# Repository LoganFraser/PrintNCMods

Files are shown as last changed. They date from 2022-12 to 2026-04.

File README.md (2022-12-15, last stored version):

# PrintNCMods
My design files for the PrintNC CNC machine

Logan BC CA - Logan#2225 on Three Design - PrintNC Discord
https://discord.gg/fXqRkUTsUD

If you like my work and want to buy me a beer (or coffee),  
you can use this [Paypal](https://www.paypal.com/donate/?hosted_button_id=QBMAY9ZB6N3F8) link    
or this QR code:  
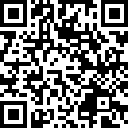
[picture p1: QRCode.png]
QRCode


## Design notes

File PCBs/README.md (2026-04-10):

## A collection of PCBs for the PrintNC compatible with various controllers ##

I sell kits for the driver key PCBs that include IDC cable, connectors, jacks and pins (5 for $20 CAD, $10 for assembly, + shipping) and a kit with the toolhead and gantry PCBs that include screw terminals, ethernet jacks ($30 CAD, $10 for assembly, + shipping) though the PrintNC Discord https://discord.gg/rXNhba3C @logan2225

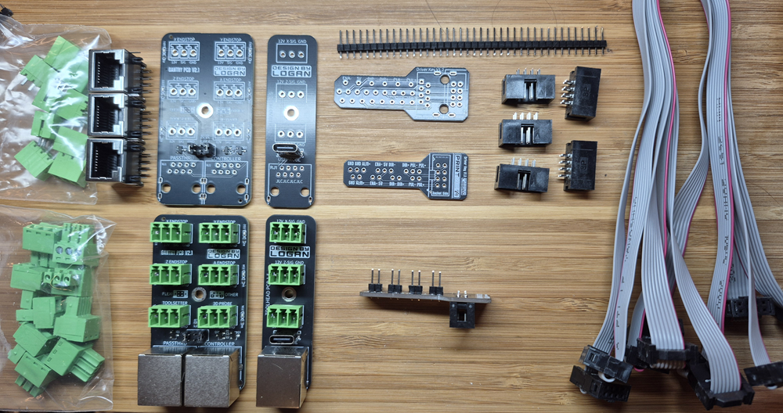
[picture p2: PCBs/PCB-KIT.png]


### Fusion 360 and Step CAD files for 3d Printed Enclosures and Soldering Guides ###
Cad files are here: https://github.com/LoganFraser/PrintNCMods/tree/main/PCBs/CAD_Sensor_PCB_Cases

### Driver Key PCB ###
A convenient method to connect the Flexihal to the DM542T/DM556T or other drivers.

Version 1.3 here: https://github.com/LoganFraser/PrintNCMods/tree/main/PCBs/Driver_Key_1.3_PCB

Version 1.2 here: https://github.com/LoganFraser/PrintNCMods/tree/main/PCBs/Driver_Key_1.2_PCB

Assembly - Use the row of pins that matches your screw terminal spacing on your stepper drivers. 
Most current open loop drivers and closed loop drives without a brake input will use the 3.81mm spacing screw terminals.  
It will be marked on one end - 3.5 or 3.81 or 5.08.  Be careful to place the IDC connector on the same side as the outline
and with the notch lined up with the silkscreen - facing away from the pins for 1.2, and towards the pins for 1.3

### Endstop PCBs: ###
a collection of pcbs that provide various functions as follows: 

### Gantry Sensor PCB ### 
 
Updated with bypass jumpers to remove the inverting effect of the LED isolation circuit for the Flexihal

https://github.com/LoganFraser/PrintNCMods/tree/main/PCBs/Gantry_Sensor_PCB_2.1

### Toolhead Sensor PCB ###
for connecting X/Z axis and 3d probe at the toolhead to minimize individual cables in the cablechain.  

https://github.com/LoganFraser/PrintNCMods/tree/main/PCBs/Toolhead_Sensor_PCB_1.5

### Sensor Endstop Cabinet PCB ###
for connecting the cabinet end of the ethernet cable. Not needed for connection to GrblHal2k EST or FlexiHAL controllers.

https://github.com/LoganFraser/PrintNCMods/tree/main/PCBs/Enclosure_Sensor_PCB

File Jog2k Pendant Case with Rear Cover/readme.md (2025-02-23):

This modifies the great case by mikemacwillie from here: 

https://github.com/Expatria-Technologies/Mods-Accessories/tree/main/Expatria/Jog2K_Deluxe

I've moved the cover to the rear of the case to make it easier to install the screen and heatset screw inserts.  

There's a screen brace that holds the screen into the case.

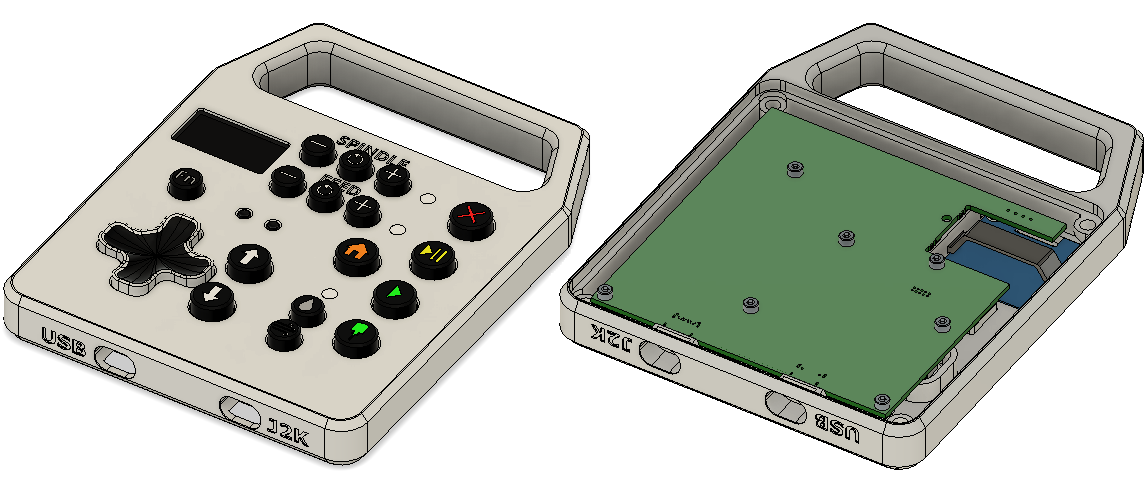
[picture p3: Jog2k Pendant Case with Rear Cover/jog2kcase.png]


This is a collection of mounts for storage of the jog2k, button pcb, and wireless or small keyboard (I use a Logitech K400)

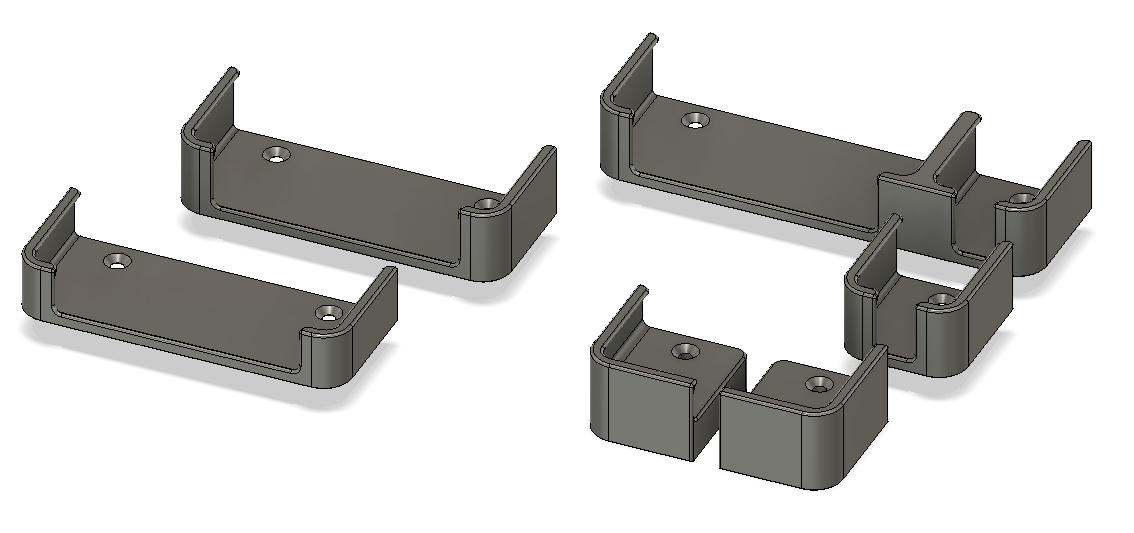
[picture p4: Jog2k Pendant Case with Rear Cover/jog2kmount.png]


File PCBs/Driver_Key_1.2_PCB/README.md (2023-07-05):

## Driver Key PCB for DM542T and DM556T

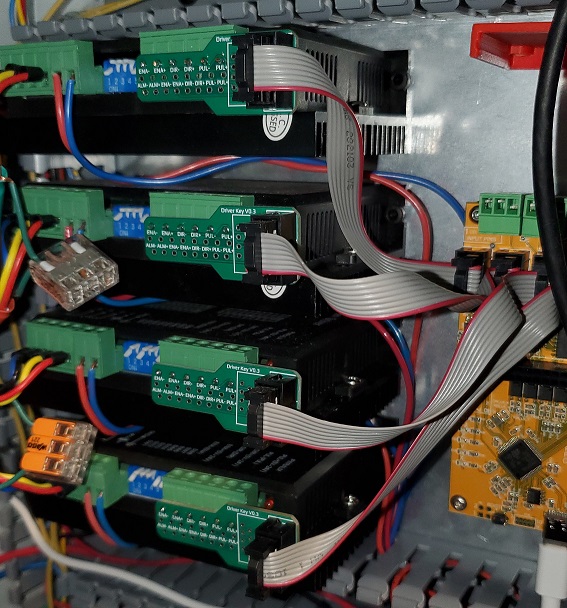
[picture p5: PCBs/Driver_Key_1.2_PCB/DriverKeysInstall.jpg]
Driver Keys Install


Goal: To provide a simple connection method from Flexihal or Grblhal 2000 IDC outputs to external drivers.

# Assembly: 

First solder the IDC 8 pin connector to the PCB, matching the silkscreen notch to the connector notch.  
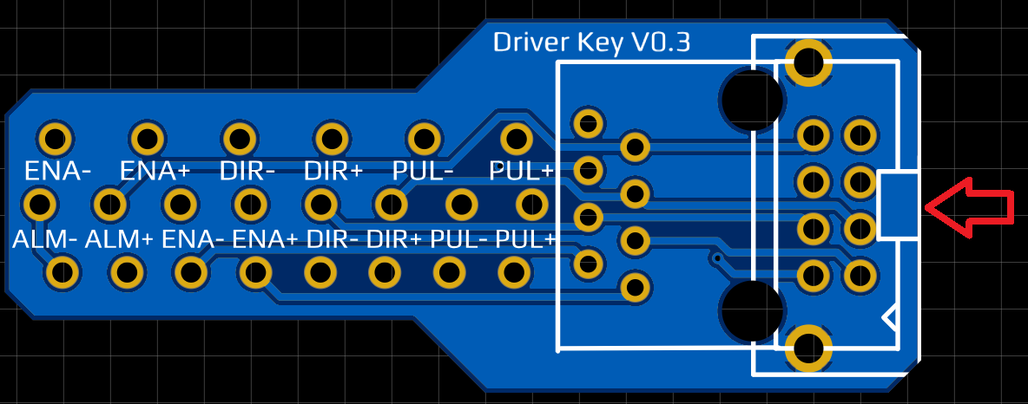
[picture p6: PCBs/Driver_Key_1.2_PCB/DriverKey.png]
DriverKey


Next remove the plugin screw terminal from the driver that has Enable, Direction and Pulse/Step inputs on it.  

Cut short pieces of 0.5mm^2/20AWG of bare(stripped) solid core wire 10mm or 3/8" long, insert into the Dir +/- and Step +/- screw terminal block and tighten the screws.

Next align the wires with the holes on the pcb that match the correct spacing, and solder in place.
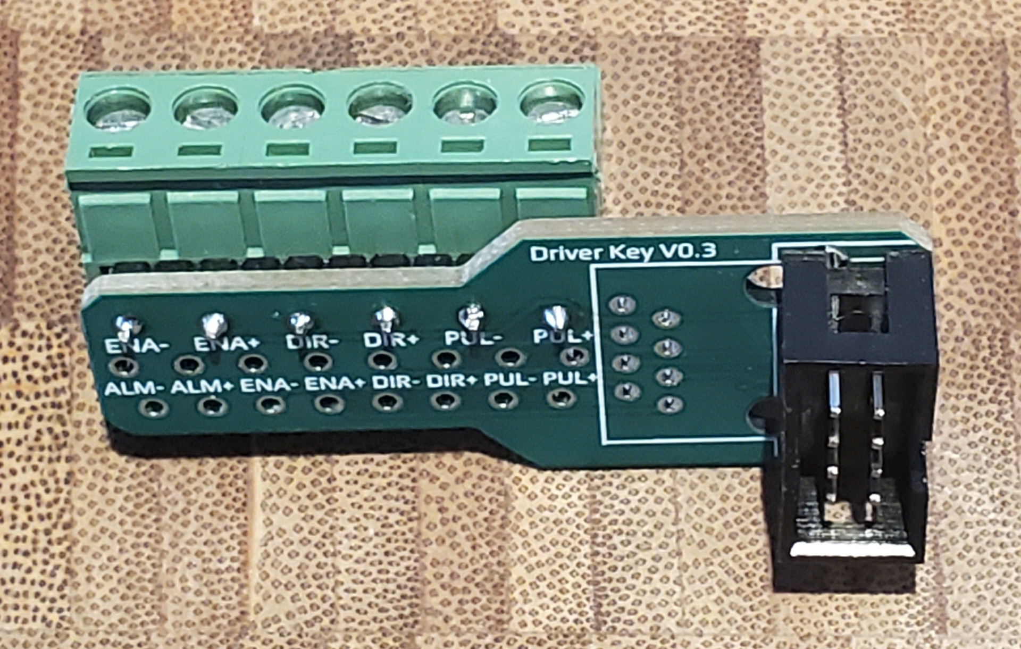
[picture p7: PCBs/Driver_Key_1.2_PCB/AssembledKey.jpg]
AssembledKey


Optional: Add wires for Enable and/or Error to the driver.  Currently neither is recommended for inital setup as it just adds confusion and doesn't provide a benefit with DM542T or DM556T drivers. 

Follow this guide to assemble the IDC cables, taking care to match the faint arrow with the red wire on both ends.  Use of a vice isn't required for 8pin idc, though, you can just press them together with a block of wood or metal on a countertop.  [IDC ribbon Cable Guide](https://startingelectronics.org/articles/IDC-ribbon-cable/)

Enjoy!  

As a bonus, here are the default jumpper settings for the PrintNC with 100 steps/mm for XYZ and 3A kit steppers on printed mounts.  

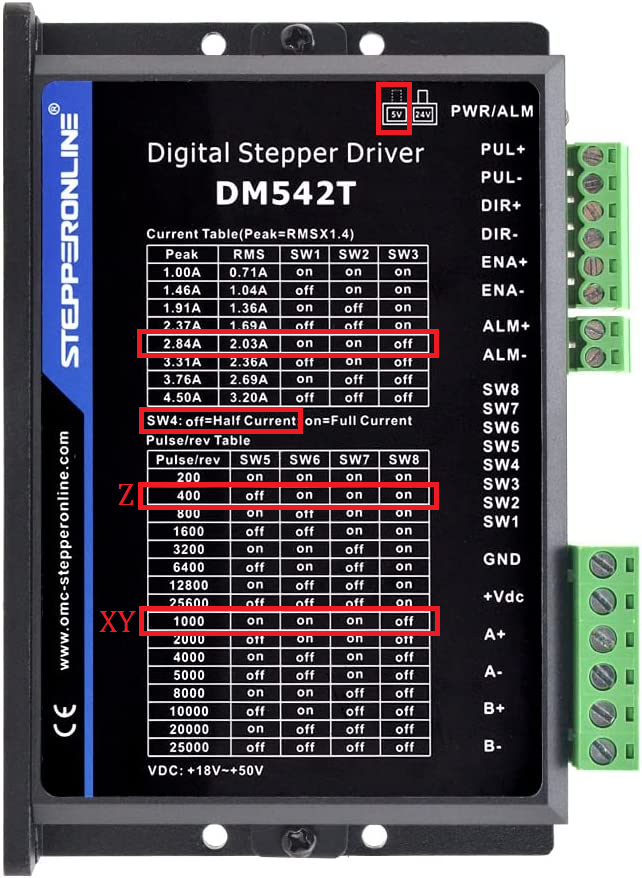
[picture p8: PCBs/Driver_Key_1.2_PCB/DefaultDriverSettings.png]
Default Driver Settings


Logan BC CA - Logan#2225 on Three Design - PrintNC Discord
https://discord.gg/fXqRkUTsUD

If you like my work and want to buy me a beer (or coffee),  
you can use this [Paypal](https://www.paypal.com/donate/?hosted_button_id=QBMAY9ZB6N3F8) link    
or this QR code:  
QRCode

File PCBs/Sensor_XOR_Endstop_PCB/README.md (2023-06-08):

## Sensor XOR Endstop PCB

This is my universal design for the PrintNC or other CNC machine connection for sensor/switch endstops using a single ethernet cable for simplicity. It's directly compatible with the pinout for the Grblhal2000 EST and Flexihal controller boards, and by using a Cabinet Breakout PCB you can connect it to other controller designs.

This PCB has a supply voltage range of 12V to 18V due to the XOR IC.  While it's possible it'll work at higher voltages I cannot provide any warranty or guarantee of function. 

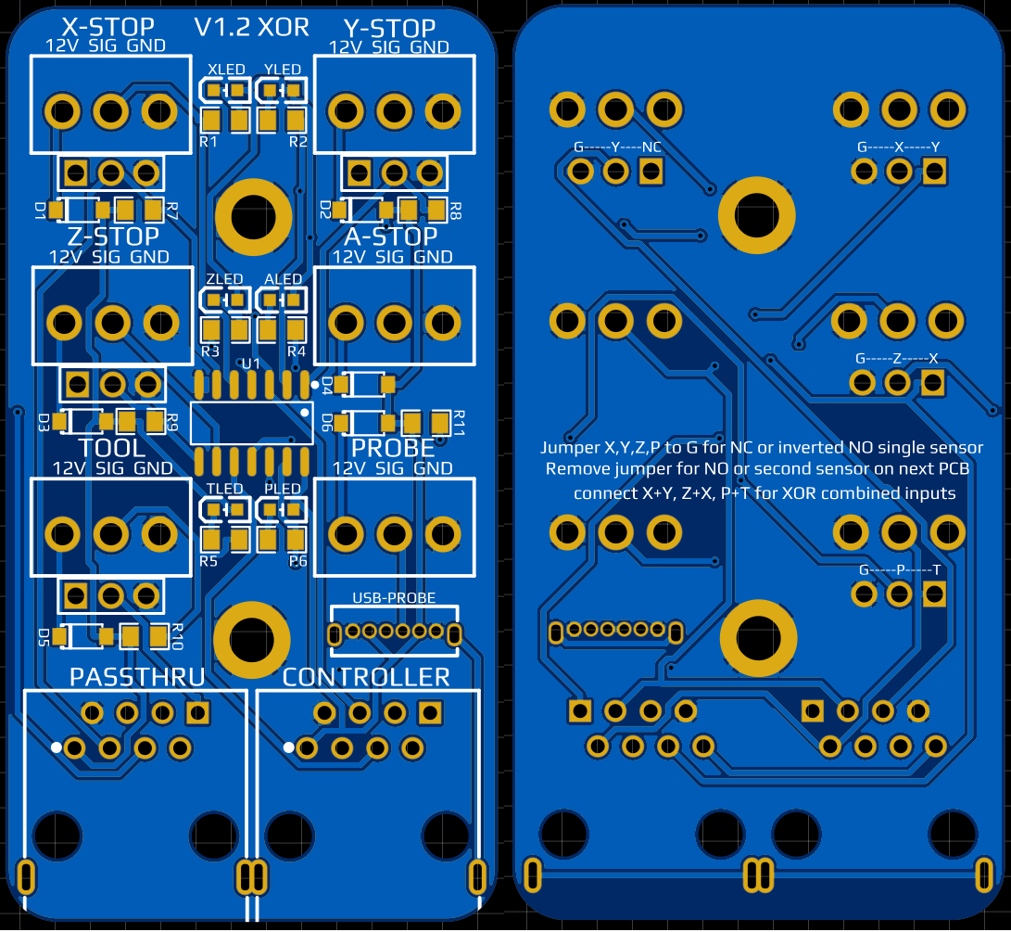
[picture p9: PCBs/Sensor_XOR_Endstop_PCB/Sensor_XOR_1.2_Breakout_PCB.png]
PCBfrontback


# Main Benefits: 

Compact design, passthrough jack for series connection to second PCB if desired, XOR gate connection to either passthough PCB for X, Y, Z, and Probe, or jumpered connections between X+Y, X+Z, and Tool+Probe for input limited controllers; parallel breakout board based cncs for example. 

# Default configuration: 
Flexihal or Grblhal 2k EST with NPN-NC sensors and a single endstop PCB: The jumpers below each of the X,Y,Z,and Probe screw terminals are connecting the passthough connection to ground to provide an active low signal so when combined with a NPN-NC input, an active low (monitored) output will result from the XOR IC gate. 

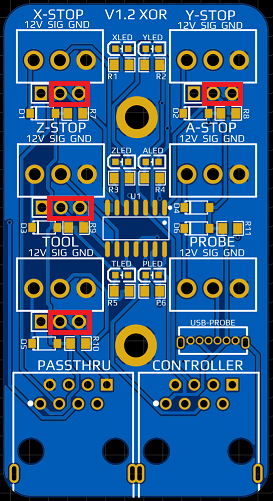
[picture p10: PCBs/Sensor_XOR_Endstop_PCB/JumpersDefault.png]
JumpersDefault


# PicoBob Configuration:
NPN-NC sensors for XYZA, Probe + Toolsetter and a single endstop PCB: X and Y are connected to Ground for the passthough input, and Z is jumpered to X and Toolsetter is jumpered to Probe to combine the inputs.

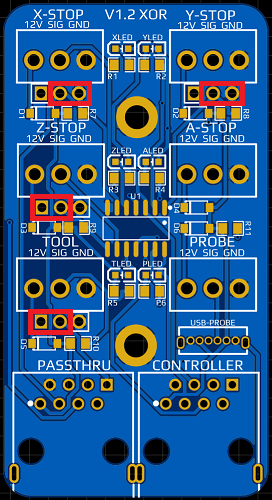
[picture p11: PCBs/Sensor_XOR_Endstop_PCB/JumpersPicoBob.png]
JumpersPicoBob


For other controllers or customizing for multiple PCBs or NO sensors:
-  Jumper X,Y,Z,P to G for NC or inverted NO single sensor
-  Remove jumper for NO or second sensor on next PCB
-  Connect X+Y, Z+X, P+T for XOR combined inputs

Logan BC CA - Logan#2225 on [Three Design discord](https://discord.gg/fXqRkUTsUD)

If you like my work and want to buy me a beer (or coffee),  
you can use this [Paypal](https://www.paypal.com/donate/?hosted_button_id=QBMAY9ZB6N3F8) link    
or this QR code:  
QRCode

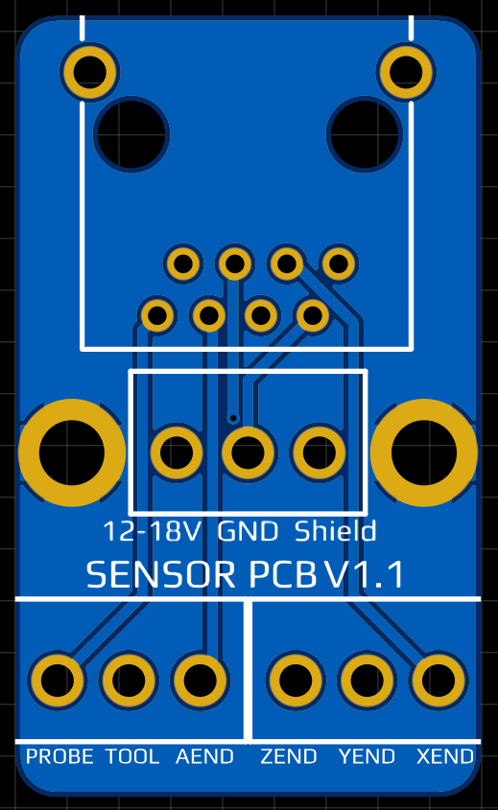
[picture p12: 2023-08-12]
PCBs/Enclosure_Sensor_PCB/SensorEndstopCabinet.png

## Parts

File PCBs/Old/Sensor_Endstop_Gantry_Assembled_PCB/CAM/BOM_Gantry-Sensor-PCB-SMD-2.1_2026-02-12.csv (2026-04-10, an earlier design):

ID | Name | Designator | Footprint | Quantity | Manufacturer Part | Manufacturer | Supplier | Supplier Part | Price
1 | HC-PZ200-8.7L-2X4PZ | H2 | HDR-TH_8P-P2.00-V-M-R2-C4-S2.00 | 1 | HC-PZ200-8.7L-2x4PZ | HC(虹成电子) | LCSC | C27985163 | 0.038
2 | AO3400A_C700953 | Q1,Q2 | SOT-23-3_L2.9-W1.3-P1.90-LS2.4-BR | 2 | AO3400A | HUASHUO(华朔) | LCSC | C700953 | 0.039
3 | MMBT5401_C2828453 | Q3 | SOT-23-3_L2.9-W1.4-P1.90-LS2.4-TR | 1 | MMBT5401 2L | CBI(创基) | LCSC | C2828453 | 0.013
4 | HC-RJ45-058-1-4 | RJ1,RJ2 | RJ45-TH_HC-RJ45-058-1-4 | 2 | HC-RJ45-058-1-4 | HCTL(华灿天禄) | LCSC | C3000196 | 0.168
5 | 3.3kΩ | R1,R2,R3,R4,R5,R6,R9 | R0402 | 7 | CR0402FF3301G | LIZ(丽智电子) | LCSC | C100376 | 0.001
6 | 100kΩ | R7,R8 | R0402 | 2 | SCR0402F100K | VO(翔胜) | LCSC | C3015887 | 0.001
7 | XL-1005UGC | LED1,LED2,LED3,LED4,LED5,LED6 | LED0402-RD_GREEN | 6 | XL-1005UGC | XINGLIGHT(成兴光) | LCSC | C965793 | 0.008
8 | KF2EDGV-3.5-3P | A,P,T,X,Y,Z | CONN-TH_3P-P3.50_KF2EDGV-3.5-3P | 6 | KF2EDGV-3.5-3P | KEFA(科发) | LCSC | C441322 | 0.075

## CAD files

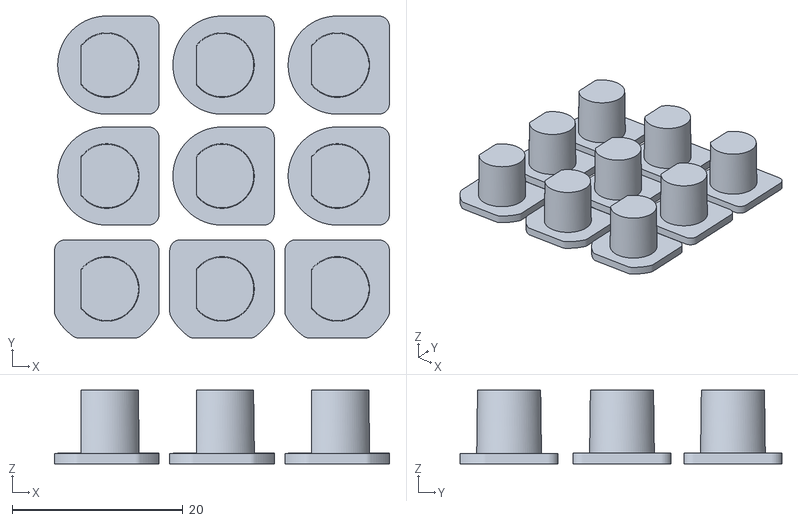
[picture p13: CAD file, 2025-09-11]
Jog2k Pendant Case with Rear Cover/STLs/White FDM Buttons.stl
39.3 x 37.7 x 8.66

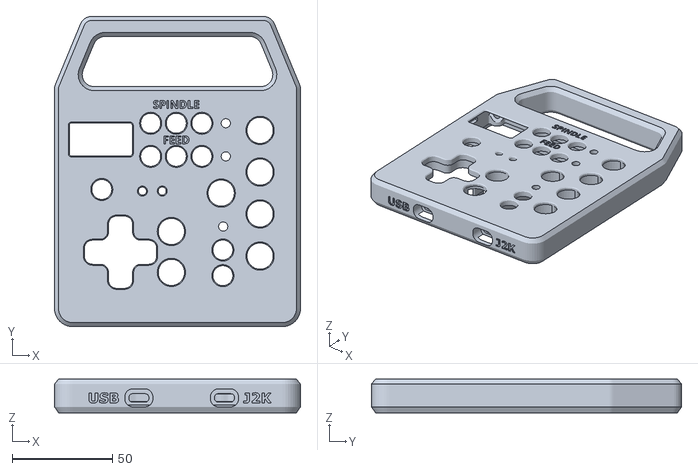
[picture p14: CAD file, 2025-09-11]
Jog2k Pendant Case with Rear Cover/STLs/Slim Enclosure.stl
122.5 x 154.5 x 16.9

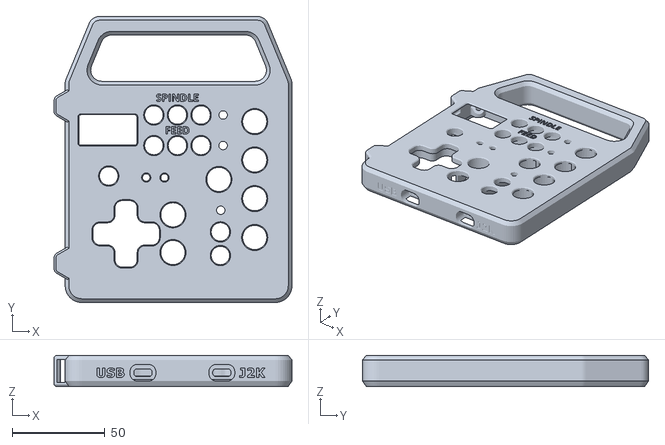
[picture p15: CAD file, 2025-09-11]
Jog2k Pendant Case with Rear Cover/STLs/Slim Enclosure w Left Side Strap.stl
128.6 x 154.5 x 16.9

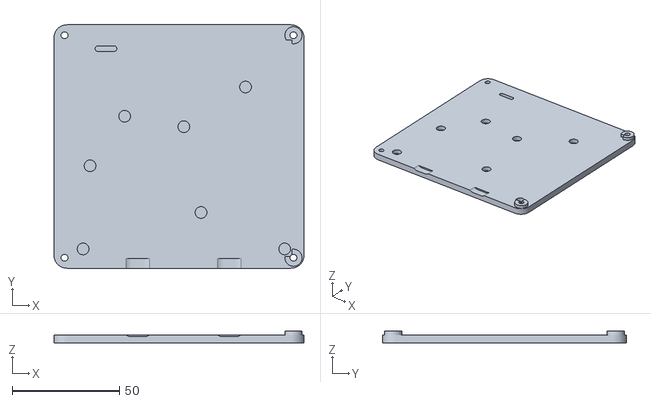
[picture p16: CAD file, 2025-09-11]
Jog2k Pendant Case with Rear Cover/STLs/Bottom Cover.stl
116.5 x 113.5 x 5.76

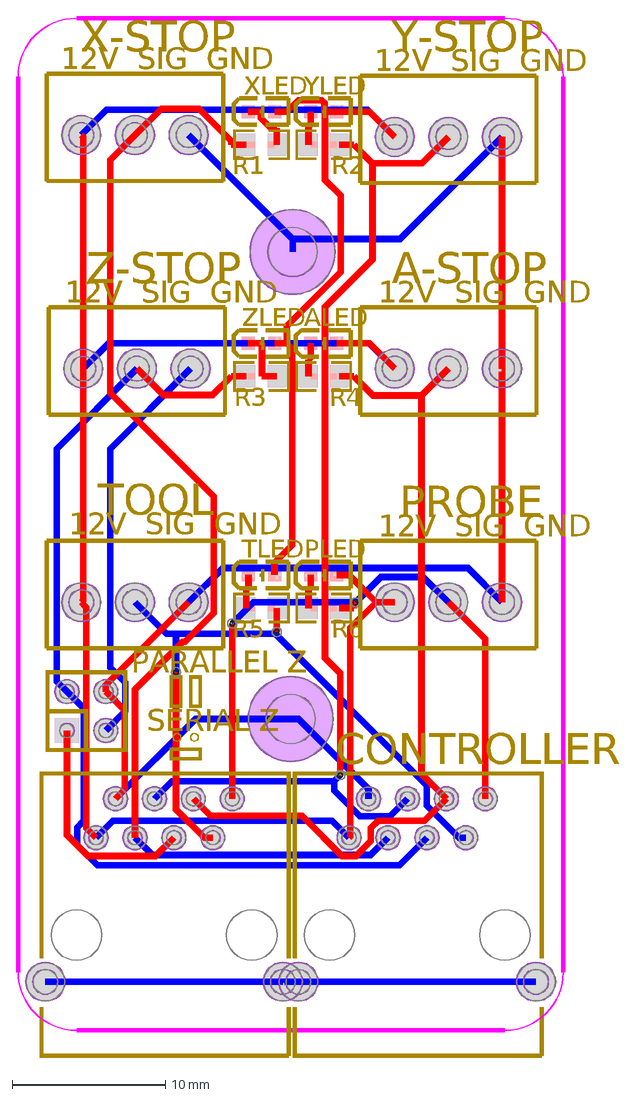
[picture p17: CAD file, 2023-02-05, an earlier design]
PCBs/Old/Sensor_Endstop_Gantry_PCB/EasyEDA Source Files/PCB_Sensor Universal_2023-02-04.dxf
12V SIG GND
CONTROLLER
PARALLEL Z
SERIAL Z
ALED
PLED
TLED
XLED
YLED
ZLED
R1
R2
R3
R4
R5
R6
PROBE
X-STOP
Z-STOP
TOOL
A-STOP
Y-STOP

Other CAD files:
Jog2k Pendant Case with Rear Cover/Pendant and Button PCB mount v9.f3d
PCBs/Old/Sensor_Endstop_Toolhead_PCB/3dPrintedCase/Sensor_PCB_Enclosure_Toolhead_V1.f3d
PCBs/Sensor_Endstop_Toolhead_Assembled_PCB/3dPrintedCase/Sensor_PCB_Enclosure_Toolhead_V1.f3d

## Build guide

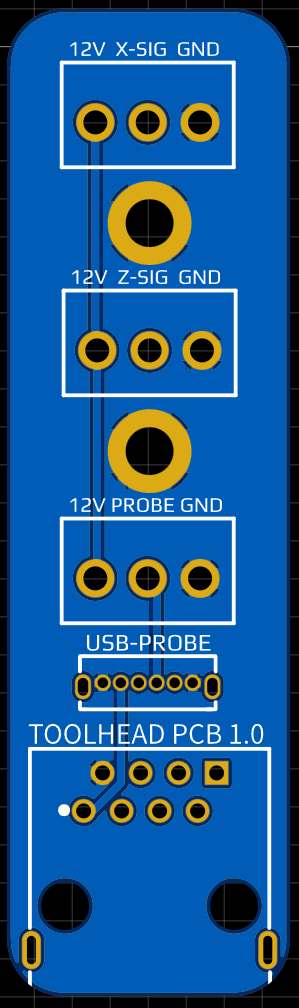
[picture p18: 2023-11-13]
PCBs/Sensor_Endstop_Toolhead_Assembled_PCB/SensorEndstopToolheadPCB.png

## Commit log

2022-07-11 Started adding rj45 adapter PCBs
2022-08-13 Updated pcbs
    [PickAndPlace_PCB_GrblHAL2k Driver to RJ45 adapter_2022-08-12.csv]
2022-08-13 Added mesa to ethernet adapter pcbs
    [PickAndPlace_PCB_Mesa PCB_2022-08-13.csv]
2022-08-14 updated pcbs to match grblhal2k est pinout
    [PickAndPlace_PCB_Mesa Endstops_2022-08-14.csv]
2022-08-15 Added source and pcb ordering files
    [PickAndPlace_PCB_Sensor Frame_2022-08-15.csv, PickAndPlace_PCB_Sensor Gantry_2022-08-15.csv, PickAndPlace_PCB_Sensor Toolhead_2022-08-15.csv]
2022-09-03 Create ihsv57 servos
    adapter board to rj45
2022-11-11 added flexihal adapter pcb
2022-11-11 All pins passed directly through for future compatibility (no sharing 5V)
2023-02-04 Replaced old design with universal
    Archived old separate PCBs for frame, gantry and toolhead to Old folder and added source and ordering files for JLCPCB for the new design featuring LEDs.
    [PickAndPlace_PCB_Sensor Frame_2022-08-15.csv, PickAndPlace_PCB_Sensor Gantry_2022-08-15.csv, PickAndPlace_PCB_Sensor Toolhead_2022-08-15.csv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]
2023-02-05 Added PCBs and Case for Passthrough endstop PCB
    [Lightpipe(clear).stl, Lower Case.stl, PCB_Sensor Universal_2023-02-04.dxf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]
2023-03-29 Uploaded Readme and CAD file.
2023-04-07 Reworked the cable chain and sensor mounts.
2023-04-09 Updated readme and fixed collision between long sensors and the roller.
2023-04-18 Added +/- to the upper case and a new upper case for the XOR pcb
    [Sensor_PCB_Enclosure_Universal v10.f3d, Sensor_PCB_Enclosure_Universal v8.f3d, Upper Case XOR.stl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]
2023-06-04 Started XOR PCB documents
2023-06-08 Create Sensor_PCB_Enclosure_Universal v15.f3d
2023-06-09 V61 fixes issue with 100mm height gantry and cable chain sketches.
2023-06-11 Tweaks to cable zip tie plate
2023-06-16 Added driver key assembly instructions
2023-06-16 File cleanup
    [BOM_PCB_breakout board for servo_2022-09-03.csv, PCB_PCB_breakout board for servo_2022-09-03.json, PickAndPlace_PCB_breakout board for servo_2022-09-03.csv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]
2023-07-05 Added Source and Gerber files for XOR 1.2 PCB
    [PickAndPlace_PCB_Sensor_XOR_1.2_2023-05-21.csv]
2023-08-07 Parameters added for chain supports.
2023-08-12 Renamed directory
    [Lightpipe(clear).stl, Lower Case.stl, PCB_Sensor Universal_2023-02-04.dxf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]
2023-08-12 Added Cabinet PCB
2023-09-04 Create Electronics Enclosure Kit v65.f3d
2023-09-18 Create Dual HGH15CA Carriage Z Axis v82.f3d
    Added latest file - has parametric chain supports so can be used for different widths and hole spacings.
2023-11-28 updated versions and added files for Z endstop pcb
    [Lightpipe(clear).stl, Lower Case.stl, Sensor_PCB_Enclosure_Toolhead_V1.f3d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]
2023-11-28 renamed directories for clarity
    [PCB_Sensor Universal_2023-02-04.dxf, PickAndPlace_PCB_Sensor Frame_2022-08-15.csv, PickAndPlace_PCB_Sensor Gantry_2022-08-15.csv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]
2023-12-17 Added direct plug pcb design.
    [PickAndPlace_PCB_Flexihal Direct-Plug Driver to RJ45 adapter_2023-12-17.csv]
2023-12-30 Updated gerber files for minor adjustments
2024-03-20 Create Gerber_PCB_Driver_Key_PCB_3.5_3.8_5.0_2024-03-19.zip
    Update DriverKey silkscreen
2024-09-13 Updated PCB source and CAM files
    [BOM_FlexiSD_2024-09-11.csv, BOM_Gantry-Sensor-PCB-SMD-6x-1.9_2024-09-11.csv, BOM_Toolhead-Sensor-PCB_2024-09-11.csv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]
2024-10-19 Restore DIY PCB
    [PCB_Sensor Universal_2023-02-04.dxf, PickAndPlace_PCB_Sensor Frame_2022-08-15.csv, PickAndPlace_PCB_Sensor Gantry_2022-08-15.csv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]
2024-12-14 Added jog2k pendant case
    [Pendant and Button PCB mount v9.f3d]
2025-02-23 added extra ground for drivers with 9 pins (brake input)
2025-03-28 Added assembled driver key for 3.5 pitch screw terminal.
    [BOM_Driver_Key_PCB_3.5_assembled_2025-03-27.csv, PickAndPlace_PCB_Driver_Key_PCB_3.5_2025-03-27.csv]
2025-04-09 Added assembled driver key 3.8
    [BOM_Driver_Key_PCB_3.8_assembled_2025-04-08.csv, PickAndPlace_PCB_Driver_Key_PCB_3.8_2025-04-08.csv]
2025-09-09 Updated PCB files and Jog2k case
    [BOM_Gantry-Sensor-PCB-SMD-2.0_2025-07-05.csv, BOM_Gantry-Sensor-PCB-SMD-2.0_2025-07-06.csv, BOM_Toolhead-Sensor-PCB_2025-07-06.csv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]
2025-09-11 Added STL files for jog2k case
    [Bottom Cover.stl, Slim Enclosure w Left Side Strap.stl, Slim Enclosure.stl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]
2025-10-25 Added directory for printed cases
    [Sensor_PCB_Cases v28.step]
2025-12-20 Added source files for V2.0 Assembled gantry sensor PCB
2026-04-10 PCB Cleanup
    [BOM_Driver_Key_PCB_3.5_assembled_2025-03-27.csv, BOM_Driver_Key_PCB_3.8_assembled_2025-04-08.csv, BOM_FlexiSD_2024-09-11.csv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]
2026-04-10 Update README with Driver Key PCB version links
    Added links to Driver Key PCB versions in README.
2026-04-10 Update PCB kit description in README
    Removed 'leds and resistors' from the kit description for toolhead and gantry PCBs.
